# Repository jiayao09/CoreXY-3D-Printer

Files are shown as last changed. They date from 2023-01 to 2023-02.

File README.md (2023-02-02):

# CoreXY Structure 3D Printer
## Overview
- Core XY structure design, full belt drive, higher stability and printing accuracy, ensure the quality of the model; 
- Dual Z-axis design, increase the bearing capacity of the hot bed, reduce errors in printing, and print more finely. 
- Customizable print range, automatic creation of drawings and parts with Siemens NX
- Capable of building the ideal 3D printer for a beginner. Additionally, it is remarkably convenient for future part upgrades.




Figure 1: Solidwork 3D model with default size 200mm x 300mmx 280mm

## Design Characteristics
### Customizable Print Range (Include everything you need)
- Bill of materials for assembly and purchase. (View the attached BOM file)

BOM

- STL file for 3D printing (Considering the different properties of the 3d printer, the model design does not leave a margin. Don't forget to modify it in the slicer software in accordance with the printing device.)
- 3D model can be changed according to set parameters for later installation and display (check out the following video)

https://user-images.githubusercontent.com/110358483/216223192-5d7ee592-2c5e-4510-852f-c61db8b9a21d.mp4

### Better Stability Made of Firm Metal
- Full metal structure.
- The machine is more stable.
- The printing accuracy is higher.


### Double Z-axis Build Bed Structure
- More stable and solid for large size prints



### Print Head Assembly
- Equipped with Ender 3 S1 series 3D printer 
- Powerful heat dissipation function and more stable model formation. 
- Large Torque, Extrusion Force Up to 80N. More precise control of feeding withdrawal.

  

### Easy Belt Maintenance
- Easier belt alignment with a movable motor

 EE

## Further development
- Adding automated bed leveling function
- Coding for 3D printers
- Uploading installation process

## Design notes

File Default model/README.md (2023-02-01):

 Solidwork 3D model with default size 200mm x 300mmx 280mm

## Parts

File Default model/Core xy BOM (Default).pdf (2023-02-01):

Expected Print Range | | IMPORTANT
x Direction (mm) | 300 | 1. To customize the size of the hot bed, please fill in the expected printing range.
y Direction (mm) | 200 | 2. The main board only supports 180W hot bed (Include MOS tube if exceed range).
z Direction (mm) | 280 | 3. Considering the physical characteristics of thread rod, print range should not exceed 300*300.

# Assembly BOM

AESSEMBLY NAME | ITEM NAME | Dimension | Unit | Material | QUANTITY | Weight | Total weight | Phase
x axis Assembly | Linear Motion Rod Shaft (x axis) | 408 | mm Aluminum 2
| X Axis Housing (left) | | | PLA (40% filling) | 1 | 48.20 | 48.20
| X Axis Housing (right) | | | PLA (40% filling) | 1 | 48.20 | 48.20
| Button Head Socket Cap Screw | M5 X 45 | | | 2
| Button Head Socket Cap Screw | M5 x 25 | | | 2
| Idler Pulley | Teeth: 20 Bore: 5 Width: 6 | | | 2
| Idler Pulley | Teethless Bore: 5 Width: 6 | | | 2
| Long Type Linear Bearings | 8 x 15 x 45 | mm | | 2 | | | LM8LUU

y axis Assembly

T Slot 2020 Extrusion (x axis) | 460 | mm | Aluminum | 4 | | | European Standard
T Slot 2020 Extrusion (y axis) | 340 | mm | Aluminum | 4 | | | European Standard
T Slot 2020 Extrusion (z axis) | 390 | mm | Aluminum | 4 | | | European Standard
Linear Motion Rod Shaft (y axis) | 334 | mm | Aluminum | 2 | | | European Standard
Rod Housing Left 01 | | | PLA (40% filling) | 1 | 19.67 | 19.67
Rod Housing Left 02 | | | PLA (40% filling) | 1 | 10.95 | 10.95
Rod Housing Right 01 | | | PLA (40% filling) | 1 | 20.22 | 20.22
Rod Housing Right 02 | | | PLA (40% filling) | 1 | 10.95 | 10.95
Filament Holder | | | PLA (40% filling) | 1
Button Head Socket Cap Screw | M4 X 8 | | | 10
Button Head Socket Cap Screw | M4 X 22 | | | 4
Button Head Socket Cap Screw | M5 X 25 | | | 2
L Shape Flat Bracket | 80 X 80 X 1 | mm | | 12
Button Head Socket Cap Screw | M6 X 10 | | | 8
Button Head Socket Cap Screw | M4 X 6 | | | 48
Round Rubber Feet Bumpers | 20 X 20 X 22 | mm | | 4
Button Head Socket Cap Screw | M4 X 16 | | | 4
2020 Series Corner Bracket | | | Aluminum | 20
Button Head Socket Cap Screw | M5 X 10 | | | 40
Stepper Motor | | mm | Reliability Aluminum | 2 | | | Nema 17
42 Stepper Motor Mounting Plate | 42 X 42 | | | 2
Limit Micro Switch | 1A 125V | | | 1 | | | SPDT
Phillips Cross Head Screw | M3 X 8 | | | 8
GT2 Pulley | Teeth: 20 Bore: 5 Width: 6 | mm | | 2
Idler Pulley | Teeth: 20 Bore: 5 Width: 6 | mm | | 4
GT2 Timing Pulley Belt | Pitch: 2; Width: 6 | mm | | 2
T-slot Nuts | M5 | | | 42
T-slot Nuts | M4 | | | 66

z axis Assembly

z axis support 02 | | mm mm | Acrylic Sheet | 2
z axis support 03 | | | Acrylic Sheet | 2
z axis support 04 | | | PLA (40% filling) | 2 | 3.96 | 7.92
z axis support 05 | | | Acrylic Sheet | 8
Linear Motion Rod Shaft (z axis) | 390 350 5 to 8 | | | 4
T8 Thread rod | | | | 2
Flexible Couplings | | | | 2
Phillips Cross Head Screw | M2 X 13 | | | 4
Limit Micro Switch | 1A 125V | | | 2 | | | SPDT

Stepper Motor | 2 | Nema 17
Round Flange Linear Ball Bearings | 8 x 15 x 45 | mm | 4 | LM8UU
Phillips Cross Head Screw | M3 x 8 | | 8
Button Head Socket Cap Screw | M4 x 12 | | 16
Heater bed Assembly | z axis support 01 | | | Acrylic Sheet | 2
| 1020 T-Track | 477 | mm | Aluminum | 2
| Heater Bed | 300 x 200 x 3 | mm | | 1 | Ender 3 V2
| Glass Bed Upgraded Build Surface Plate | 300 x 200 x 4 | mm | | 1 | Ender 3 V2
| Heated Bed Cover | 300 x 200 | mm | | 1 | Ender 3 V2
| Flat Bracet | 40 | mm | Stainless Steel | 4
| Compression Spring | 0.5 x 5 x 40 | mm | | 2
| Compression Mould Die Springs | OD: 8 ; Length: 25 | | | 4
| Knurled Thumb Nuts | M3 | | | 6
| Phillips Cross Head Screw | M3 x 40 | | | 5
| Button Head Socket Cap Screw | M5 x 10 | | | 4
| Button Head Socket Cap Screw | M5 x 12 | | | 8
| Round Flange Linear Ball Bearings | 8 x 15 x 45 | mm | | 4 | LM8UU
| Anti-backlash Spring Loaded Nut | Pitch: 2 ; Lead: 8 | mm | | 2
| Phillips Cross Head Screw | M3 x 13 | | | 24
| Square Nut | M3 | | 304 Stainless | 24
Hot end Assembly | Hot End Full Kit | | | | 1
| Hot End Axis Holder | | | PLA (40% filling) | 1 | 32.28 | 32.28
| Hot End Holder 01 | | | PLA (40% filling) | 1 | 10.29 | 10.29
| Hot End Holder 02 | | | PLA (40% filling) | 1 | 8.63 | 8.63
| Cooling Fan Holder | | | PLA (40% filling) | 2 | 2.17 | 4.34 | Can be Print or Pruchase
| Series 3010 Cooling Fan | 30 x 30 x 10 | mm | | 1 | | | 12V
| Series 4010 Cooling Fan | 40 x 40 x 10 | mm | | 2 | | | 12V
| Long Type Linear Bearings | 8 x 15 x 45 | mm | | 2 | | | LM8LUU
| Limit Micro Switch | 1A 125V | | | 1
| Square Nut | M3 | | 304 Stainless | 6
| Phillips Cross Head Screw | M2.5 X 8 | | | 8
| Phillips Cross Head Screw | M3 X 40 | | | 2
| Phillips Cross Head Screw | M3 x 10 | | | 4
| Phillips Cross Head Screw | M2 X 13 | | | 2
| Extruder Feeder | | | | 1 | | | Ender 3 V2
| Stepper Motor | | | | 1 | | | Nema 17
| 42 Stepper Motor Mounting Plate | 42 x 42 M3 x 8 | mm | Reliability Aluminum | 1
| Phillips Cross Head Screw | | | | 4
Control board Assembly | Control board 01 | | | PLA (40% filling) | 1 | 88.95 | 88.95
| Control board 02 | | | PLA (40% filling) | 1 | 24.30 | 24.3
| SD Card | 2G | | | 1
| LCD Display Touch Panel | 240X320 with PCB 5V/3.3V | | | 1
| 3D Printer Control Board | Gen L V2.1 | | | 1
| Power Supply | 460W 12V38A | | | 1
| Stepper Motor Driver | TMC2208 | | | 5
| Spiral Cable Wrap | 6 | mm | PE | 1
| Phillips Cross Head Screw | M3 x 8 | | | 4
| Button Head Socket Cap Screw | M4 X 8 | | | 16
| T-slot Nuts | M4 | | | 16
Total weight | 334.90

# Purchase BOM

AESSEMBLY NAME | ITEM NAME | Dimension | Unit | Material | QUANTITY | Cost/Unit | Estimate Cost | Phase
Customize Part | Linear Motion Rod Shaft | 408 | mm | Aluminum | 2 | 14.99 | 29.98 | x axis
| | 334 | mm | Aluminum | 2 | 13.29 | 26.58 | y axis
| | 390 | mm | Aluminum | 4 | 14.99 | 59.96 | z axis
| T Slot 2020 Extrusion | 460 | mm | Aluminum | 4 | 7.75 | 31 | x axis
| | 340 | mm | Aluminum | 4 | 4.75 | 19 | y axis
| | 390 | mm | Aluminum | 4 | 4.75 | 19 | z axis
| 1020 T-Track | 477 | mm | Aluminum | 2 | 14.43 | 28.86
| 3D Printing Part T8 Thread rod | | g | PLA (40% filling) | 334.9 | 0.08 | 26.792
| | 350 | | | 2 | 12 | 24
| Acrylic Sheet | 297 x 420 | mm | Acrylic | 1 | 22.79 | 22.79
| Heater Bed | 300 x 200 x 3 | mm | | 1 | 28 | 28 | Ender 3 V2
| Glass Bed Upgraded Build Surface Plate | 300 x 200 x 4 | mm | | 1 | 11.59 | 11.59 | Ender 3 V2
| Heated Bed Cover | 300 x 200 | mm | | 1 | 17.99 | 17.99

Hardware

Long Type Linear Bearings | 8 x 15 x 45 | | | 4 | 3.75 | 15 | LM8LUU
Round Flange Linear Ball Bearings | 8 x 15 x 45 | | | 4 | 6 | 24 | LM8UU
2020 Series Corner Bracket | | | Aluminum | 20 | 0.575 | 11.5
L Shape Flat Bracket | 80 x 80 x 1 | mm | | 12 | 0.6 | 7.2
Flat Bracet | 40 | mm | Stainless Steel | 4 | 0.59 | 2.37
42 Stepper Motor Mounting Plate | 42 x 42 | mm | Reliability Aluminum | 3 | 2.518 | 7.554
Anti-backlash Spring Loaded Nut | Pitch: 2 ; Lead: 8 | mm | | 2 | 2.5 | 5
Compression Spring | 0.5 x 5 x 40 | mm | | 1 | 0.9 | 0.9
Compression Mould Die Springs | OD: 8 ; Length: 25 | mm | | 4 | 0.8 | 3.2
T-slot Nuts | M5 | | | 42 | 0.16 | 6.72
T-slot Nuts | M4 | | | 82 | 0.1 | 8.2
Knurled Thumb Nuts | M3 | | | 6 | 0.7 | 4.2
Square Nut | M3 | | 304 Stainless | 30 | 0.089 5 | 2.67
Flexible Couplings | 5 to 8 | mm | | 2 | | 10
GT2 Pulley | Teeth: 20 Bore: 5 Width: 6 | mm | | 2 | 1.596 | 3.192
Idler Pulley | Teeth: 20 Bore: 5 Width: 6 | mm | | 6 | 1.8 | 10.8
Idler Pulley | Teethless Bore: 5 Width: 6 | mm | | 2 | 1.8 | 3.6
GT2 Timing Pulley Belt | Pitch: 2; Width: 6 | mm | | 2 | 3 | 6
Round Rubber Feet Bumpers | 20 X 20 X 22 | mm | | 4 | 1.75 | 7
| M4 X 6 | | 304 Stainless | 48 | 0.13 | 6.33
| M4 X 8 | | 304 Stainless | 26 | 0.13 | 3.43
| M4 x 12 | | 304 Stainless | 16 | 0.14 | 2.23
| M4 X 16 | | 304 Stainless | 4 | 0.18 | 0.73
| M4 X 20 | | 304 Stainless | 4 | 0.22 | 0.88
| M5 X 10 | | 304 Stainless | 44 | 0.09 | 3.91
| M5 x 12 | | 304 Stainless | 8 | 0.09 | 0.71
| M5 X 25 | | 304 Stainless | 4 | 0.42 | 1.69
| M5 X 45 | | 304 Stainless | 2 | 0.63 | 1.25
| M6 X 10 | | 304 Stainless | 8 | 0.26 | 2.08

Button Head Socket Cap Screw

M2 X 12 | 304 Stainless | 6 | 0.13 | 0.76
M2.5 X 8 | 304 Stainless | 8 | 0.09 | 0.73
M3 X 8 | 304 Stainless | 24 | 0.14 | 3.36

Phillips Cross Head Screw | M3 x 10 | 304 Stainless | 4 | 0.14 | 0.56
M3 x 13 | 304 Stainless | 24 | 0.14 | 3.36
M3 x 40 | 304 Stainless | 7 | 0.27 | 1.86
Electronic component | Stepper Motor | | | | 5 | 8 | 40 | Nema 17
| Stepper Motor Driver | | | | 5 | 4 | 20 | TMC2208
| Limit Micro Switch | 1A 125V | | | 5 | 0.28 | 1.4 | SPDT
| Series 3010 Cooling Fan | 30 x 30 x 10 | mm | | 1 | 7 | 7 | 12V
| Series 4010 Cooling Fan | 40 x 40 x 10 | mm | | 2 | 5.5 | 11 | 12V
| Extruder Feeder | | | | 1 | 14.98 | 14.98 | Ender 3 V2
| Hot End Full Kit | | | | 1 | 15 | 15
| Spiral Cable Wrap | 6 | mm | PE | 1 | 11 | 11
| SD Card | 2G | | | 1 | 7 | 7
| LCD Display Touch Panel | 240X320 with PCB 5V/3.3V | mm | | 1 | 16.39 | 16.39
| 3D Printer Control Board | | | | 1 | 32.99 | 32.99 | Gen L V2.1
| Power Supply | 460W 12V38A | | | 1 | 30 | 30
Total Cost | 725.28

# Hot End BOM

Part Name | Dimension | Unit | Material | QUANTITY
V6 HeatSink (Long Distance) | 1.75 / 3 | mm | All-Metal | 1
V6 Heating Block | 20 x 20 x10 | mm | Aluminum | 1
Extruder Nozzles | 1.75 | mm | Brass | 1
High speed Fan Cover (for 3010) | | | | 1
Nozzle Throat | 1.75 / 3 | mm | Stainless Steel | 1
Tube Fitting | PC4-01 | | | 2
PTFE/teflon tubing | OD: 4; ID: 2 | mm | | 1
Thermistor Temp Sensor | 100K | ohm | | 2
Heat resistant & ventilation | 12V/40W NTC | | | 1

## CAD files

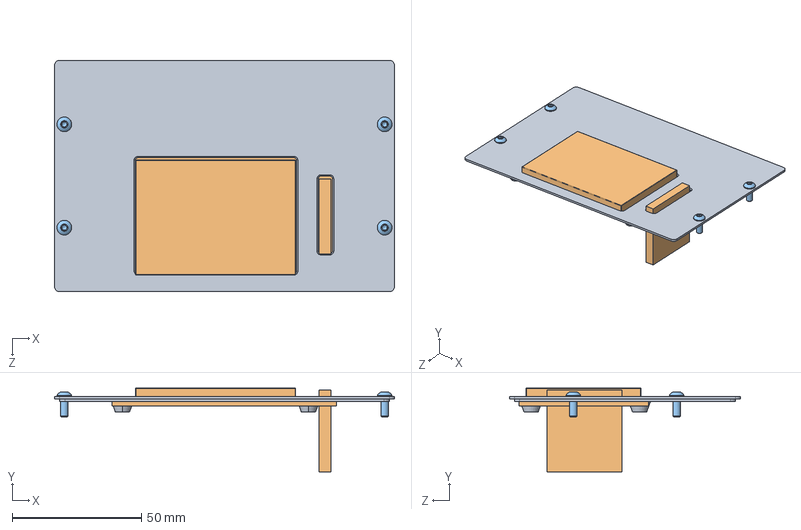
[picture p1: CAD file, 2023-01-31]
Default model/CoreXY/Control board/control bord Assembly.SLDASM
131.6 x 32.5 x 89.6 mm
control box 02
MKS_TFT24V1
socket button head cap screw_am x 4

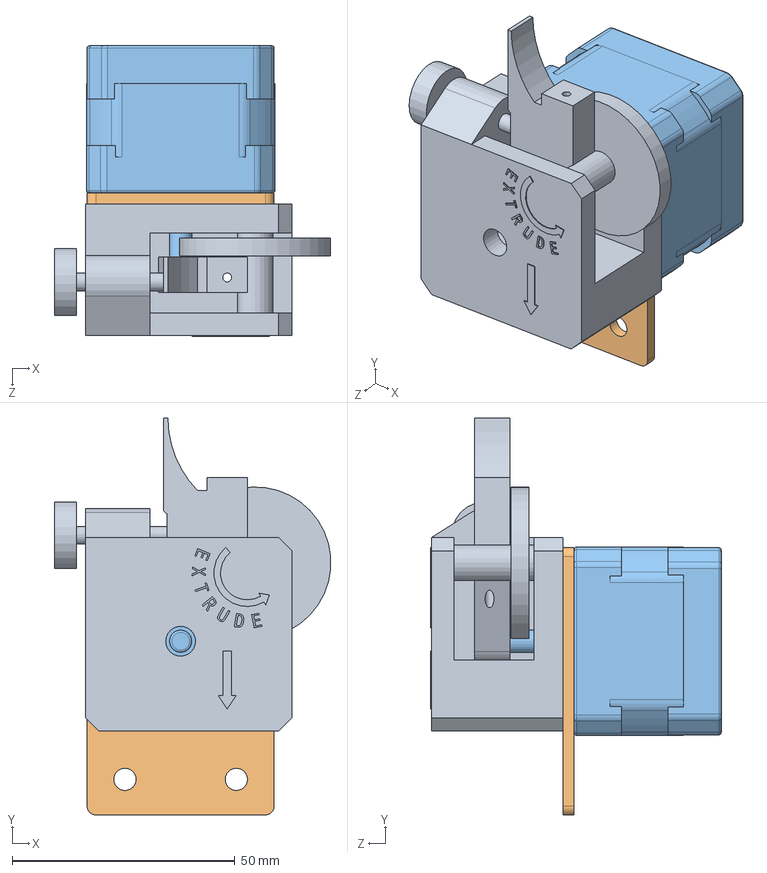
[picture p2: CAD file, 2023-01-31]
Default model/CoreXY/Hot end/hot end Assembly 02.SLDASM
62.0 x 89.1 x 65.2 mm
Extruder Feeder
motor support
Nema_17_PHB42S34-401A
socket button head cap screw_am x 4

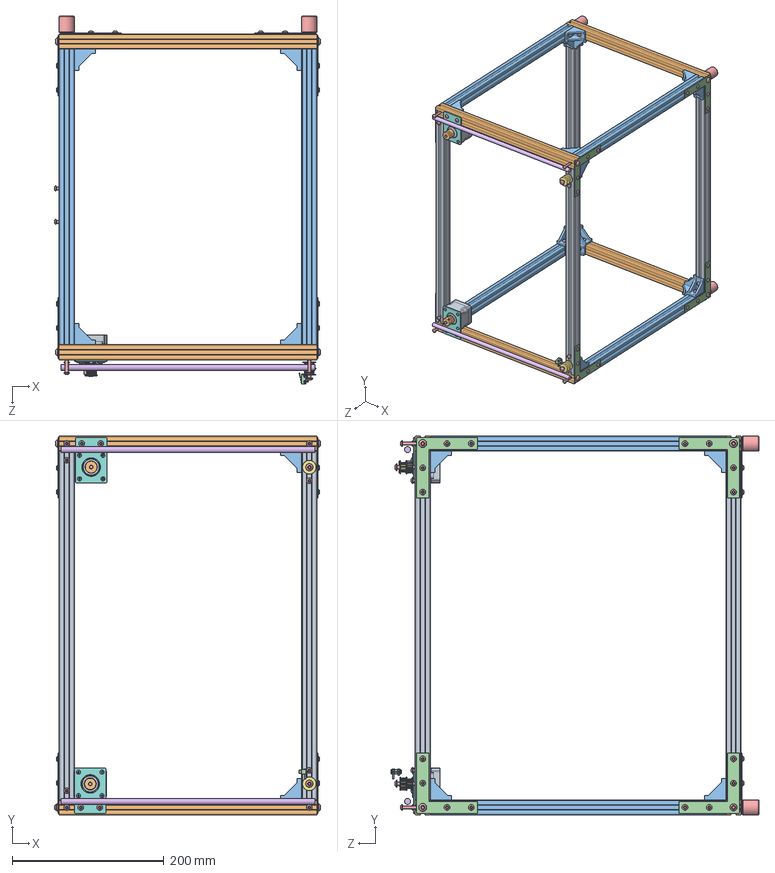
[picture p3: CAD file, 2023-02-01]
Default model/CoreXY/y axis/y axis Assembly.SLDASM
351.0 x 500.0 x 485.2 mm
2020 Aluminum x axis Extrusion x 4
2020 Aluminum y axis Extrusion x 4
2020 Aluminum z axis Extrusion x 4
Sheet metal support x 12
Base support x 4
y axis rod x 2
Idler Pulley (20 Teeth 5mm Bore 6mm Width) x 4
motor support x 2
Nema_17_PHB42S34-401A x 2
GT2_Pulley20_Teeth.stp x 2
Corner Bracket 28x28x20 for 2020 AluProfile x 20
Micro limit switch
socket button head cap screw_am1 x 116
socket set screw cone point_am x 4

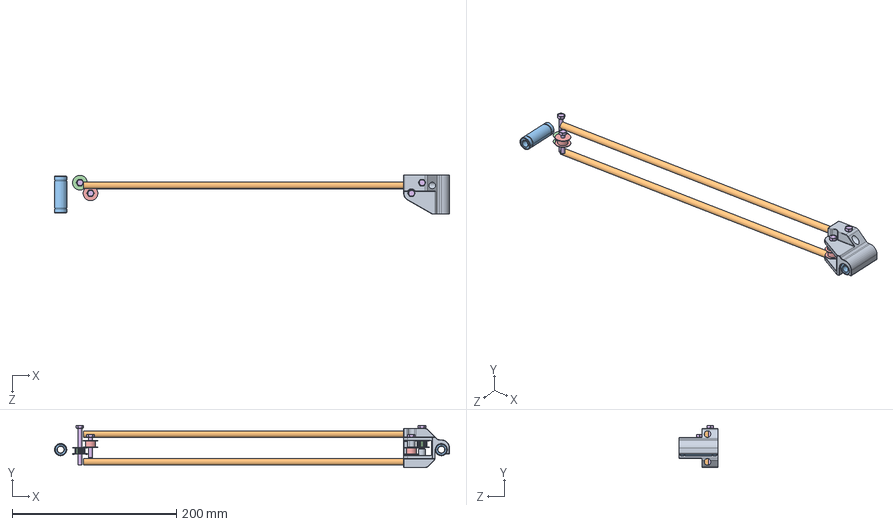
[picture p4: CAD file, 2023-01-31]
Default model/CoreXY/x axis/x axis assembly.SLDASM
481.5 x 51.7 x 48.0 mm
x axis rod x 2
x axis rod housing (right)
LM8LUU_8x15x45 x 2
Idler Pulley (20 Teeth 5mm Bore 6mm Width) x 2
Idler Pulley (Teethless 5mm Bore 6mm Width) x 2
formed hex screw_am x 4

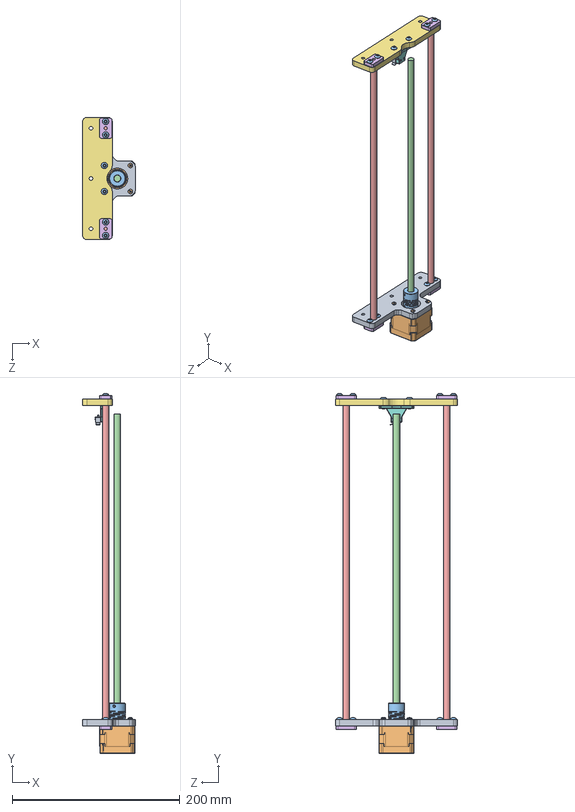
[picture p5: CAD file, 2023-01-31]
Default model/CoreXY/z axis/z axis Assembly.SLDASM
63.0 x 429.7 x 146.0 mm
z axis support 02
Nema_17_PHB42S34-401A
5mm to 8mm flexible shaft coupler
z axis thread rod
z axis rod x 2
z axis support 05 x 4
z axis support 03
z axis support 04
Micro limit switch
socket button head cap screw_am x 10
oval head_am x 2

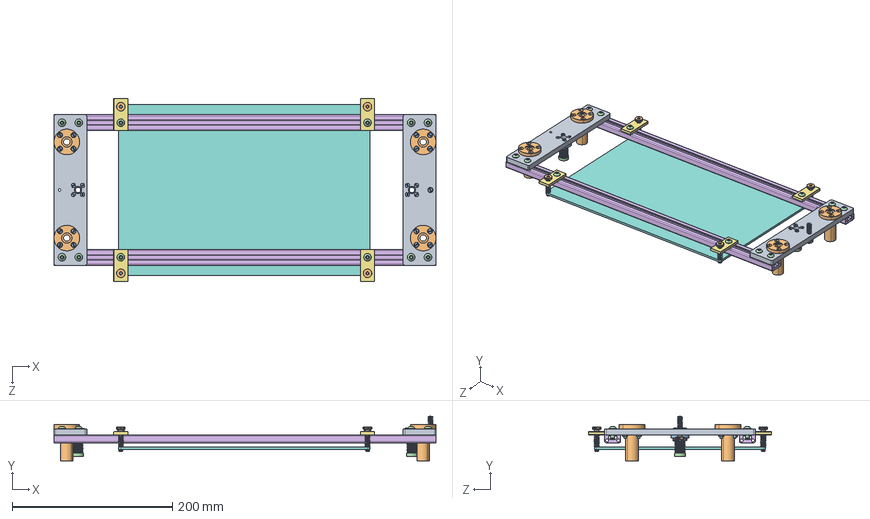
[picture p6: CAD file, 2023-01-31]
Default model/CoreXY/Heater bed/Heater bed Assembly.SLDASM
477.0 x 55.7 x 228.0 mm
z axis support 01 x 2
LMEF8LUU_8x15x45 x 4
MainBody.step x 2
TensionBody.step x 2
Spring.step x 2
1020 Aluminum Extrusion x 2
heating bed support x 4
printing board
spring for 3d printer x 5
M3 knurled thumb nut x 5
socket button head cap screw_am x 12
hex nut style 1_am x 23

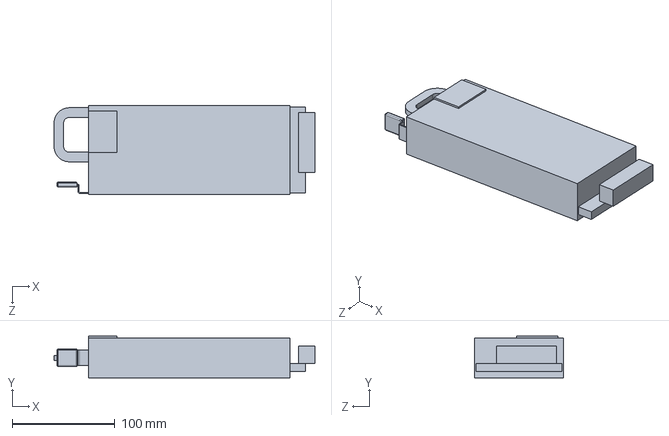
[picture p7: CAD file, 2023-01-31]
Default model/CoreXY/Battery.SLDPRT
254.5 x 40.5 x 86.5 mm

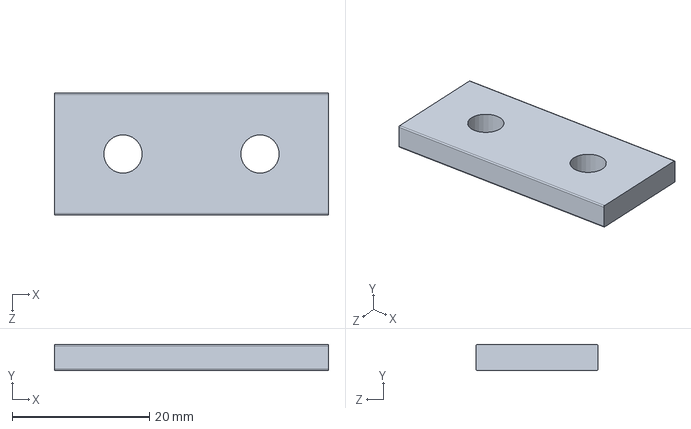
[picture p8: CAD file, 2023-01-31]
Default model/CoreXY/Heater bed/heating bed support.SLDPRT
40.0 x 3.80 x 17.8 mm

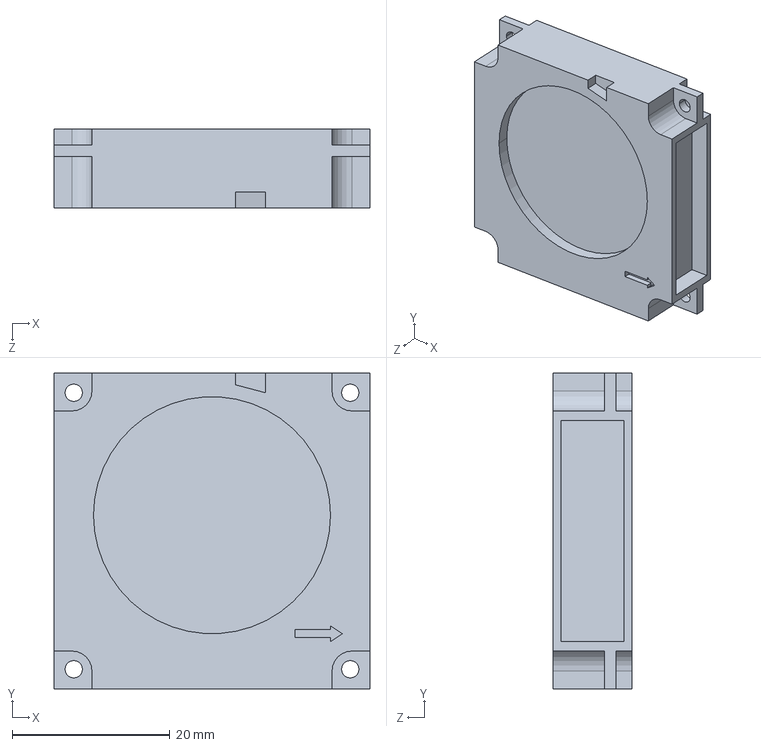
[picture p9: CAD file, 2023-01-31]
Default model/CoreXY/Standard part/turbofan_4010.SLDPRT
40.0 x 40.0 x 10.0 mm

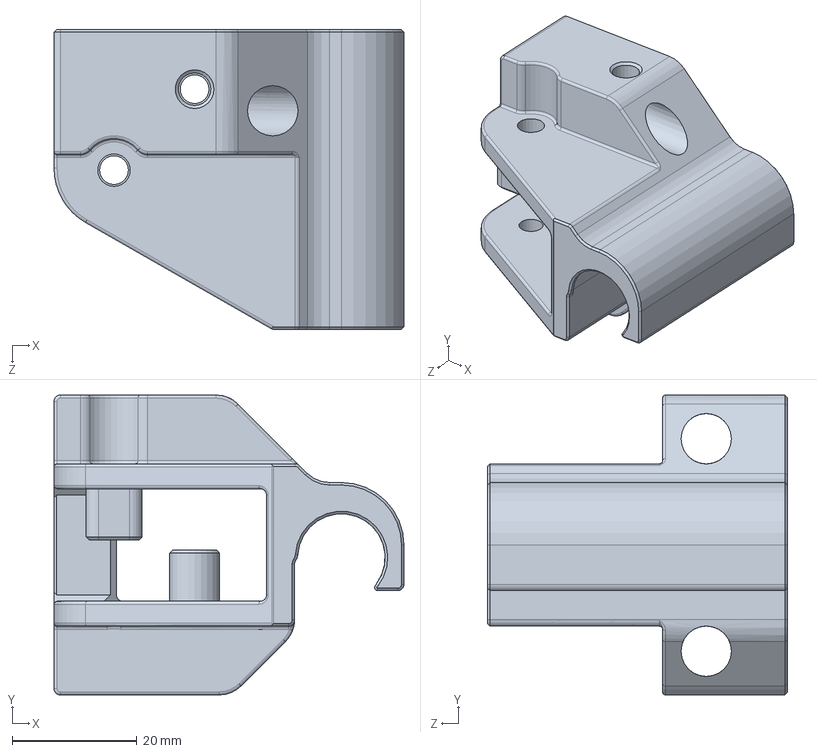
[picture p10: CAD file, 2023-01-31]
Default model/CoreXY/x axis/x axis rod housing (right).SLDPRT
56.0 x 48.0 x 48.0 mm

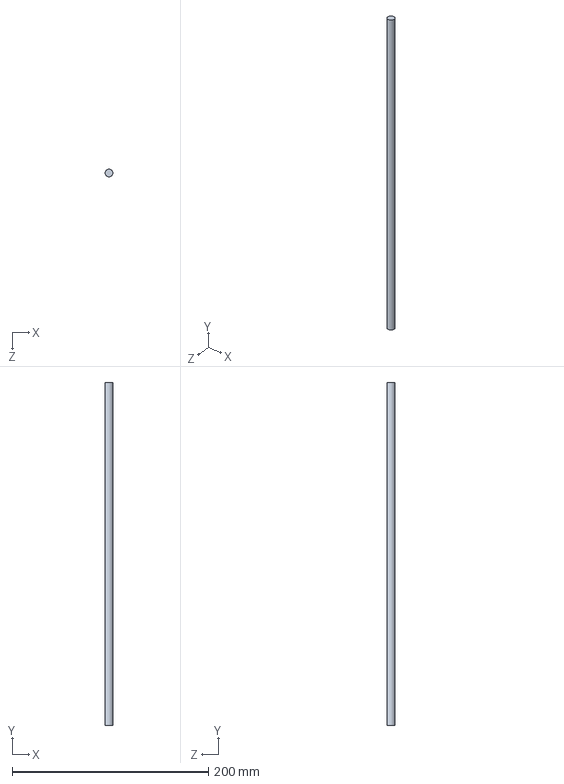
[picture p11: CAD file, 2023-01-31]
Default model/CoreXY/z axis/z axis thread rod.SLDPRT
8.00 x 350.0 x 8.00 mm

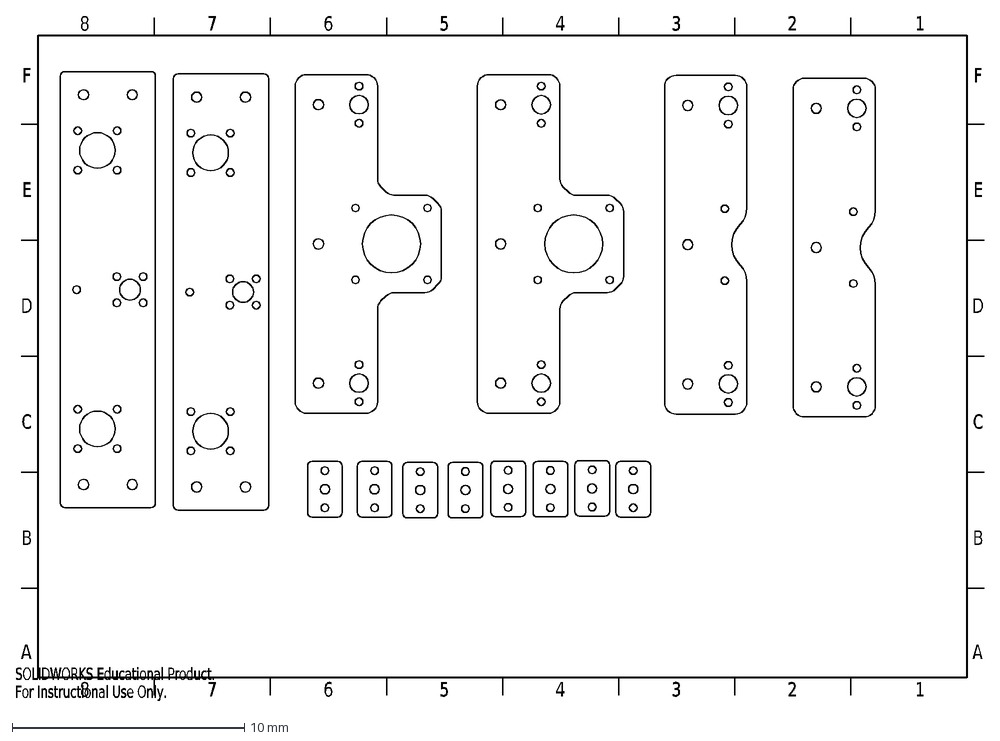
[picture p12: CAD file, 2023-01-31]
Default model/Laser cutting drawing (default).DXF
A
B
C
D
E
F
8
7
6
5
4
3
2
1
SOLIDWORKS Educational Product.
For Instructional Use Only.

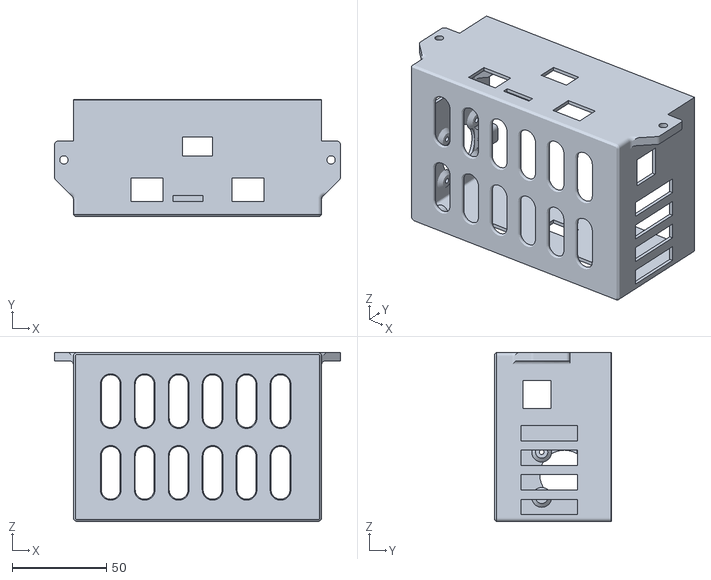
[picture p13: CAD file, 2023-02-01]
STL 3d printed part/control box 01.STL
151.6 x 62.0 x 89.6

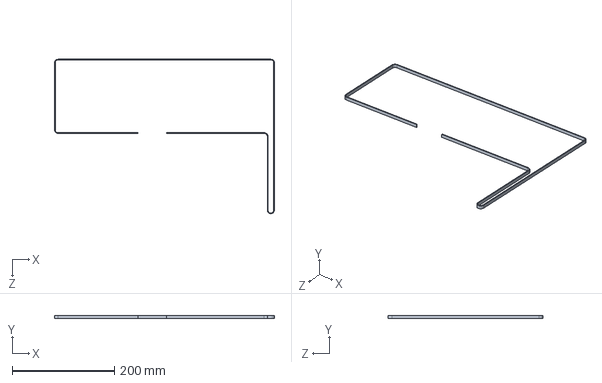
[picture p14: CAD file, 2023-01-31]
Default model/CoreXY/Belt 01.SLDPRT
431.1 x 6.00 x 302.8 mm

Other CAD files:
Default model/CoreXY/Control board/control box 02.SLDPRT
Default model/CoreXY/Heater bed/1020 Aluminum Extrusion.SLDPRT
Default model/CoreXY/Hot end/cooling fan holder.SLDPRT
Default model/CoreXY/Standard part/MKS_TFT24V1.SLDPRT
Default model/CoreXY/Belt 02.SLDPRT
Default model/CoreXY/Control board/control box 01.SLDPRT
Default model/CoreXY/Heater bed/printing board.SLDPRT
Default model/CoreXY/Heater bed/z axis support 01.SLDPRT
Default model/CoreXY/Hot end/hot end holder 02.SLDPRT
Default model/CoreXY/Hot end/hot end holder.SLDPRT
Default model/CoreXY/Hot end/hot end xy axis holder.SLDPRT
Default model/CoreXY/Laser cutting drawing (default).SLDDRW
Default model/CoreXY/Standard part/1020 Aluminum Extrusion.IGS
Default model/CoreXY/Standard part/2020 Aluminum Extrusion.IGS
Default model/CoreXY/Standard part/5mm to 8mm flexible shaft coupler.SLDPRT
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
